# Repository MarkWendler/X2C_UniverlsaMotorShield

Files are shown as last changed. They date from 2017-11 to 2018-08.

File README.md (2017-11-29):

# X2C_Motorshield
Universal motor driver board for X2C Development board

## Planned Main features
* BLDC, PMSM motor drive
* 2 Phase Current sense
* 3 Phase voltage sense
* Led feedback from PWM outputs                                                                   
* Over current protection
* Optional Motor supply (Up to 48V Not)
* Interface to HALL sensor and Quadrature Encoder
* DC common current sens
* External OPAMP
* CAN Bus

## Recommended parts
* MOSFET:	DMT4002LPS			http://www.diodes.com/_files/datasheets/DMT4002LPS.pdf						
* Mosfet Driver:	MIC4607			http://www.microchip.com/wwwproducts/en/MIC4607						
* Current and voltage sense:	MCP6024 http://www.microchip.com/wwwproducts/en/MCP6024						
* 5V Supply LDO:	MCP1790/91									
* 8-12V LDO:	MIC5233 (Adjustable)			http://ww1.microchip.com/downloads/en/DeviceDoc/mic5233.pdf						
* CAN transciever:	ATA6563

### Pinout
Coming soon

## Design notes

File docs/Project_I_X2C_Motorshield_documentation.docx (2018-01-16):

# X2C Universal motor shield

Authors:

Csányi Dániel (Obuda university)

Mark Wendler

mark.wendler@microchip.com

Christoph Baumgartner

christoph.baumgartner@microchip.com

V 0.1

15.01.2018

RECOMMENDED READING

X2C development board docs:

- http://x2c.microstickplus.com/home

# 1 Introduction

With the X2C motor driver development board we can control a BLDC (brushless DC) motor or a permanent magnet synchronous motor (PMSM). This Motorshield is a separate board from the X2C+ Development Board and this board is not contained microcontroller. The control unit is a X2C+ development board, integrated Pickit on Board programmer/debugger support. The main motor control device unit is a 16-bit dsPIC33EP256MC502.

This document is showed the Motorshield board without the X2C features.

  1.1 Features overview

The key features of this board include the following:

- Motor Control Interfaces
- Three-phase inverter bridge with a power rating 48V/15A
- Hall sensors/quadrature encoder interface for sensored motor control
- Phase voltage feedback for sensorless BLDC operation
- DC bus current sesnse resistor for single shunt vector control
- Phase current sense resistor for dual shunt vector control
- Overcurrent protection
- Support for dsPIC DSCs with internal and external op amps
- Input/Output Control Switches
- LED indicators for EN/FLT
- LED indicators for PWM input
- Jumpers for sense
- Communication ports
- CAN interface port
- Power Supply Connectors
- 24V power input connector (Shield)
- Test Points

# 2 Hardware overview

This part describes the hardware components of the X2C Motorshield. The Motorshield panel works only with the X2C+ Development Board. X2C Development board is the main control unit to provide the control signals for the motor shield.

Topics covered include:

- The schematic circuit (Attached in the supplement)
- X2C board
- Parts of shield
- Pin configuration
- Board connectors

## 2.1 X2C Board

X2C+ Development Board is a cost-effective development board. The Development Board is designed to provide designers with an easy to use, economical development environment for 8 bit PIC Microcontrollers (PIC16F1885x and PIC18F2xK40), 16-bit dsPIC Enhanced Digital Signal Controllers (dsPIC33E), 16 bit PIC Enhanced Microcontrollers (PIC24E) and 32 bit PIC Microcontrollers (PIC32MX1, PIC32MM) manufactured in 28-pin SPDIP packing. It’s the perfect solution to those looking for a low-cost, easy-to-use development platform.

Some features:

- Onboard programmer/debugger PKOB
- Onboard peripherals
- No external power supply needed
- Suitable size
- Low cost

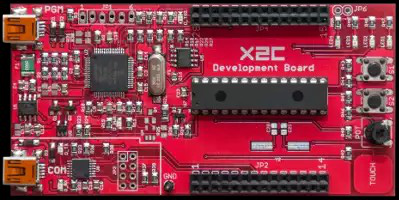
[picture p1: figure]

1. picture: X2C Development Board

The development Board is compatible with MPLAB X IDE. The software can run on PC to develop applications. It works at easy as Plug and Play, only connect the device to the PC and download the program to X2C. The Motorshield is had to connect to X2C Development Board that it is would be work.

## 2.2 Parts of shield

The schematic circuit to separate into some main subunits according to their function.

These subunits:

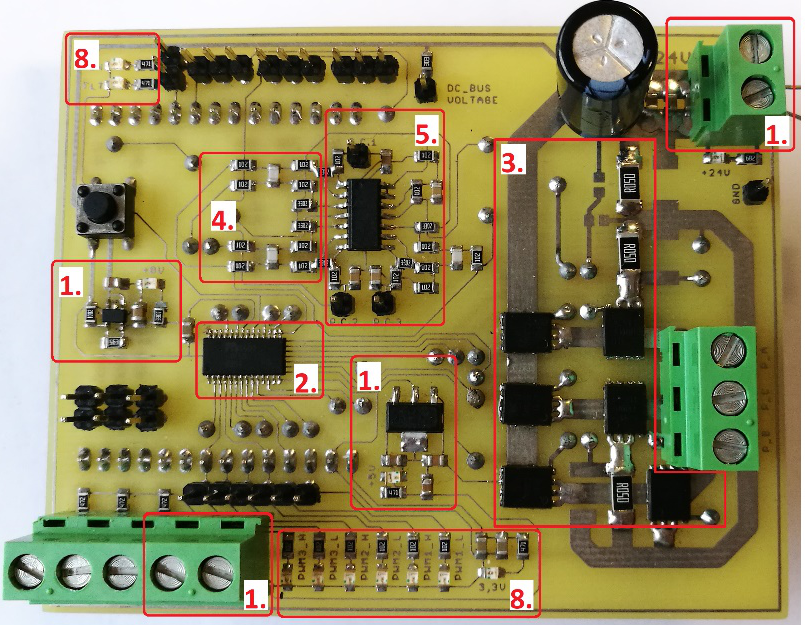
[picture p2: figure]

1. Supply

2. picture: Parts of Motorshield

2. Mosfet driver
3. Output stage
4. Phase voltage feedback
5. Current gain
6. Hall and QEI sensor

(on the other side of shield)

7. CAN Bus

(on the other side of shield)

8. Supply and output feedbacks

### Supply

External supply up to 48V is required, because high output power is needed. The capacitors stabilize the voltage and filter external noises.

The second supply convert the voltage to 5V from 24V. The MCP1790 regulator provides up to 70 mA of current. The regulator has a tight tolerance output voltage load regulation of ±0.2% and a very good line regulation at ±0.0002%/V. The regulator output is stable with electrolytic capacitors.

Voltage level | Voltage source | User part
24V | External | MOSFET
8V | Regulator | MOSFET driver
5V | Regulator | Leds, CAN, Motor sensors (CAN, HALL)
3.3V | X2C | X2C, driver’s FLT pin, Current gain

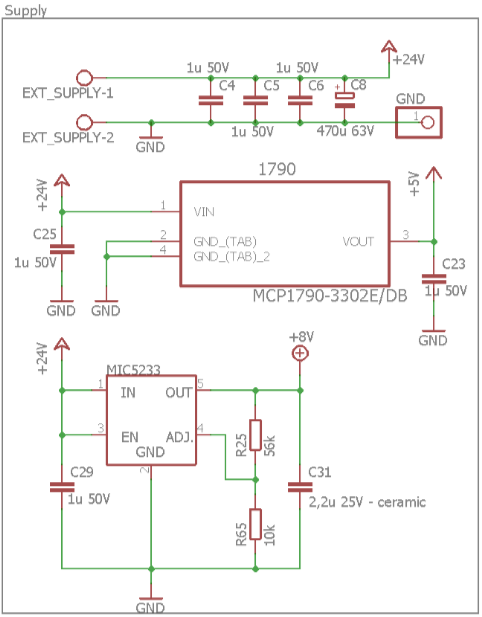
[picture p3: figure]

3. picture: Supply and regulators

The third voltage is the 8V, that use to Mosfet driver’s input voltage. The MIC5233 is a 100mA highly accurate, low dropout (270mV at 100mA) regulator with high input voltage. It only requires a 2.2uF capacitor for stability.

The sensors use a fourth voltage level – 3.3V, that support the X2C board.

### Mosfet driver

The three-phase Mosfet driver is a MIC4607. It features adaptive dead time and fast (35ns) propagation delay time and designed to independently drive six N-channel MOSFETs in a three phase bridge. Single PWM inputs can be separate high and low drive generated internally. High- and low-side outputs are guaranteed to not overlap in either mode. The driver includes overcurrent protection as well as a high-voltage internal diode that charges the high-side gate drive bootstrap capacitor. The programmable overcurrent protection circuit turns off all outputs during an overcurrent fault. Undervoltage protection is provided on both the low- and high side drivers. The input voltage is 8V from the regulator. The small switcing times that about 35ns, become a fast driver.

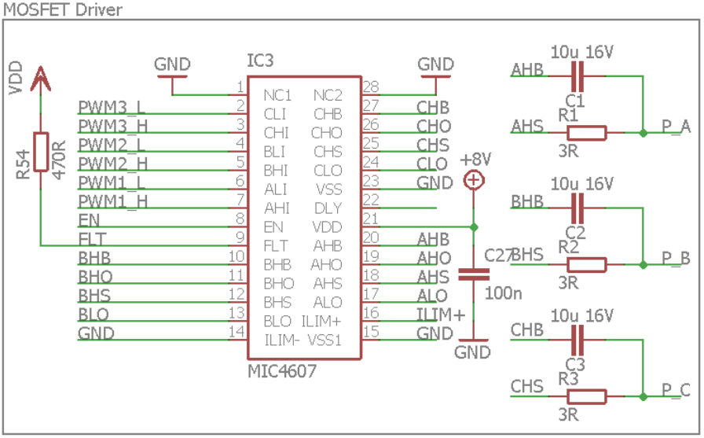
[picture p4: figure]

4. picture: MOSFET driver

There is one external enable pin that controls all three phases. A logic high on the enable pin (EN) allows for startup for all phases and normal operation. Conversely, when a logic low is applied on the enable pin, all phases turn-off and the device enters a low current shutdown mode. All outputs (xHO and xLO) are pulled low when EN is low.

FLT pin open-drain output is pulled low while the gate drive outputs are latched off after an over-current condition. It will de-assert once the DLY pin has reached the V_(DLY+) threshold and a rising edge occurs on any LI pin. During normal operation, the internal pull-down MOSFET is of the pin is high impedance. A pull-up resistor must be connected to this pin.

All input pins (xLI and xHI) are referenced to the VSS pin. The MIC4607 has a TTL-compatible input range and can be used with input signals with amplitude less than the supply voltage. The threshold level is independent of the VDD supply voltage and there is no dependence between I_(VDD) and the input signal amplitude. This feature makes the driver an excellent level translator that will drive high level gate threshold MOSFETs from low-voltage PWM IC.

On the right side of the picture the external output signals attached to driver via bootstrap capacitor and a resistor. The ceramic condensator filter the noises.

Pin number | Pin Name | Pinout description
2 | CLI | Low-Side Input for Phase C
3 | CHI | High-Side Input for Phase C
4 | BLI | Low-Side Input for Phase B
5 | BHI | High-Side Input for Phase B
6 | ALI | Low-Side Input for Phase A
7 | AHI | High-Side Input for Phase A
8 | EN | Active high enable input
9 | FLT | Fault/pin goes low when overcurrent
11 | BHO | Phase B High Side Drive Output
13 | BLO | Phase B Low Side Drive Output
14 | ILIM- | Differential Current-Limit Input (most -)
16 | ILIM+ | Differential Current-Limit Input (most +)
17 | ALO | Phase A Low Side Drive Output
19 | AHO | Phase A High Side Drive Output
21 | VDD | Input Supply
22 | DLY | Fault Delay/connect to GND
24 | CLO | Phase C Low Side Drive Output
26 | CHO | Phase C High Side Drive Output

### Output stage

The output stage principle is a three phase voltage inverter circuit that control the Mosfet driver. The N-channel MOSFET is a DMT4002LPS with very big continuously current (100A). This MOSFET has been designed to minimize the on-state resistance ( R_(DS(ON)) ) and yet maintain superior switching performance, making it ideal for high efficiency power management applications.

Main features:

- Unclamped Inductive Switching
- Thermally Efficient Package
- High conversion Efficiency
- Low R_(DS(ON))
- Small Package Profile

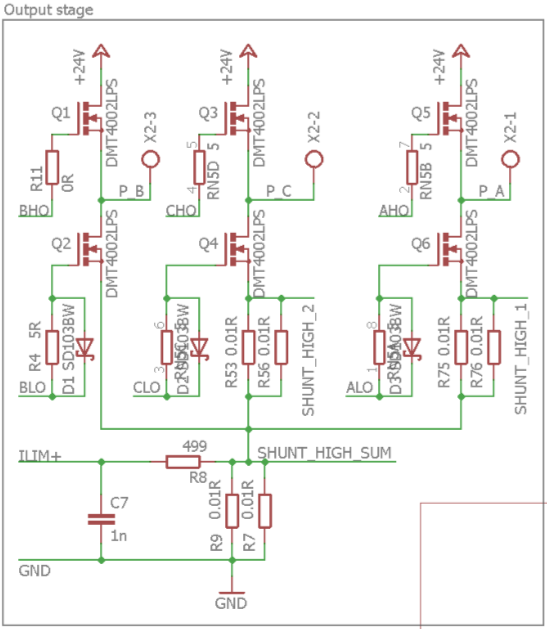
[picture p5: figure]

5. picture: Output stage

The ILIM+ and ILIM- pins provide a Kelvin-sensed circuit that monitors the voltage across an external current sense resistor. This resistor is typically connected between the source pins of all three low-side MOSFETs and power ground. If the peak voltage across this resistor exceeds the U_(ILIM+) threshold, it will cause all six outputs to latch off when the current more than 40A.

I_(max) =(U_(ILIM+))/(R_(shunt))=(200 mV)/(0.005 Ω)=40 A

Main characteristics
Characteristics | | Symbol | Value | Units
Max Drain-Source Voltage | | U_(DSS) | 40 | V
Max Gate-Source Voltage | | U_(GSS) | ±20 | V
Max Continuous Drain Current, U_(GS) =10V | T_c = +25 ℃ T_c = +70 ℃ | I_D | 100 100 | A A
Drain-Souce Breakdown Voltage | U_(GS) =0V | BU_(DSS) | 40 | V
Static Drain-Source On-Resistance | U_(GS) =10V, I_D =25A | R_(DS(ON)) | 1.3 | mΩ
Rising Overcurrent Threshold | | U_(ILIM+) | 200 | mV

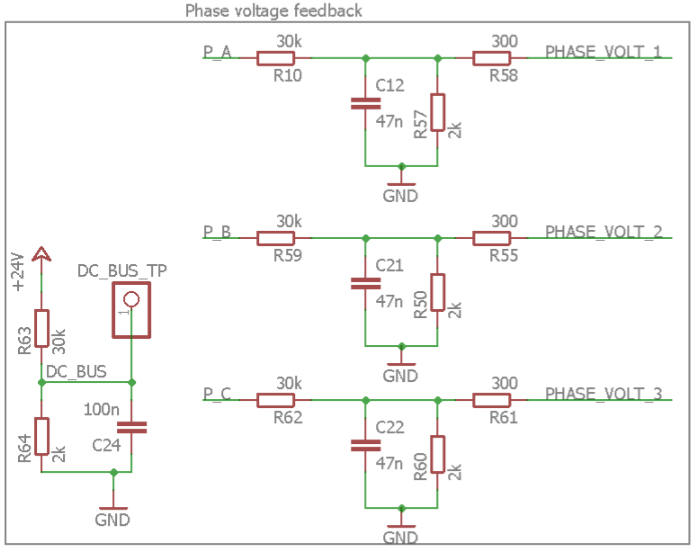
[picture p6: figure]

### Phase voltage feedback

6. picture: Phase voltage feedback

The output signals are feedbacked by resistance divider. These feedbacks are connected to dsPIC microcontroller and it is processed the analog signals. The microcontroller is measured the voltages, because if the motor hasn’t got sensors, the control is generated from the phase voltages. This part is contained a supply to DC BUS. The X2C is communicated and is exchanged data with the Motorshield panel. The data transfer is operated as serial. The data is modulated to the DC BUS.

### Current gain

The MCP6024 is rail-to-rail input and output operational amplifiers with high performance.

Main features:

- Wide Bandwidth: 10 MHz
- Low Noise
- Low Offset Voltage
- Low Supply Current
- Power supply range: 2.5V to 5.5V

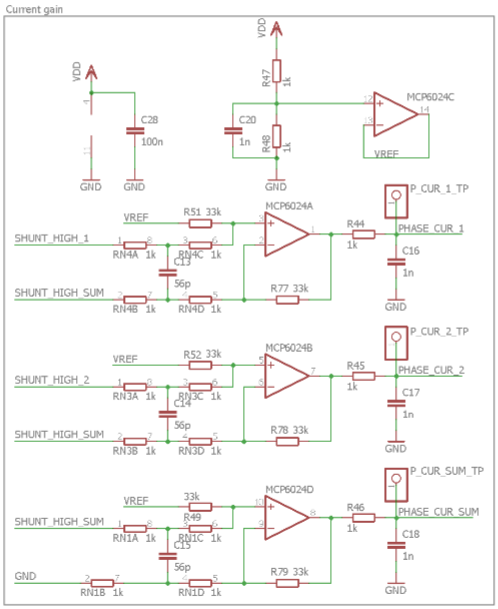
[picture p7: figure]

7. picture: Current gain

On low-side parts are measured the currents on A, C shunts and common sources level. . From the sum level is operated the overcurrent protection. In order to prevent damage and/or improper operation of these amplifiers, the circuit must limit the voltages at the input pins. The two resistros on the input side, limit the possible currents in or out of the input pins.

Circuit A (VDD to amplifier) sets the operational amplifier at its minimum noise gain. The resistor divider produces any desired reference voltage within the output voltage range of the operational amplifier. The operational amplifier buffers that reference voltage. Circuit B (Uref) uses the minimum number of components and operates as a comparator, but it may draw more current.

### Hall and QEI sensor

The most common way to control a BLDC motor is to use Hall sensors to determine the rotor position. The control system senses the rotor position and the proper voltage pattern is applied to the motor.

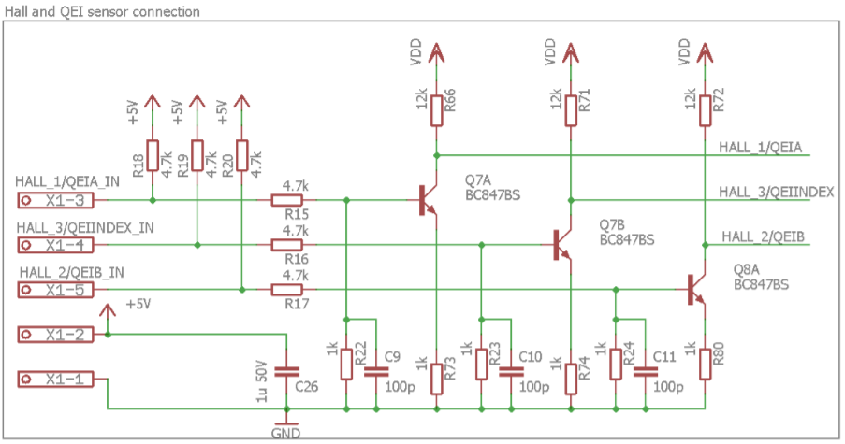
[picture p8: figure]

8. picture: Hall and QE sensor's circuit

A quadrature encoder is a type of incremental encoder used in many general automation applications where sensing the direction of movement is required. If your motor is used a large vector, a bearingless or magnetic encoder will provide the most reliable feedback. This part of circuit is contained a 5V output supply connectors.

### CAN Bus

The ATA6563 is a high-speed CAN transceiver that provides an interface between a controller area network (CAN) protocol controller and the physical two-wire CAN bus. The transceiver is designed for high-speed Can applications and providing differential transmit and receive capabillity to a CAN protocol controller.

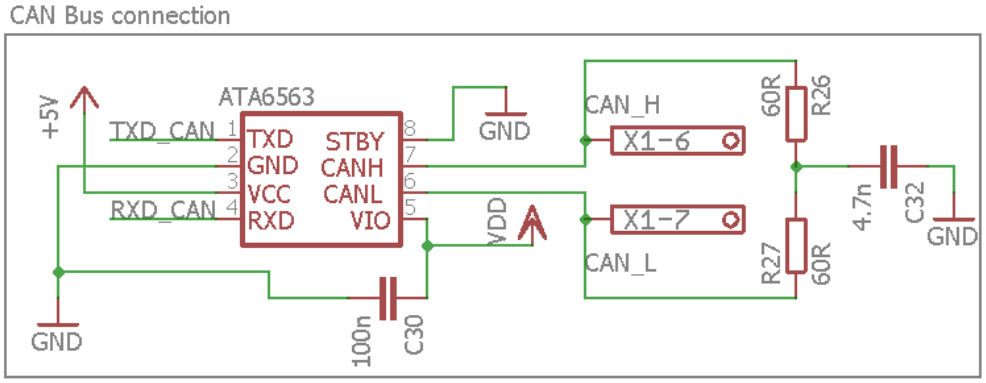
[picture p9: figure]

9. picture: Can bus circuit

The pin 5 is the VIO pin and should be connected to the microcontroller supply voltage. This allows direct interfacing to microcontrollers with supply voltages down to 3V and adjusts the signal levels of the TXD, RXD, and STBY pins to I/O levels of the microcontroller.

## 2.3 Pin configuration

Summarizes the Pin configuration for the X2C Motorshield MIC4607 driver. This table shows the dsPIC Digital Signal Controller Pin configuration. These Pins use the main board, the MOSFET driver or part of the Motorshield panel.

dsPIC | | Motorshield | | User tool | Description
Pin number | Pin name | Pin number | Signal name
1 | MCLR | L1 | GND | Used both panel | Connect to GND
2 | AN0/RA0 | L2 | Phase_I_V_2 | Used both panel | Measure voltage on Phase B or current on Phase C
3 | AN1/ RA1 | L3 | POT | X2C Board | Potenciometer
4 | PGED3/VREF-/AN2/RB0 | L4 | Phase_I_V_3 | Used both panel | Measure voltage on Phase C or current on common source point
5 | PGEC3/VREF+/RPI33/RB1 | L5 | PGEC | No connection
6 | PGEC1/AN4/RPI34/RB2 | L6 | Phase_I_V_1 | Used both panel | Measure voltage on Phase A or current on Phase A
7 | PGED1/AN5/RP35/RB3 | L7 | DC_BUS | Motorshield panel | Communicating supply
8 | VSS | L8 | GND | Used both panel | Connect to GND
9 | RA2 | L9 | EN | Motorshield panel | Active high enable input
10 | RA3 | L10 | FLT | Motorshield panel | Fault/pin goes low when overcurrent
11 | RP36/RB4 | L11 | | No connection
12 | RP20/RA4 | L12 | | No connection
13 | VDD | L13 | NC | X2C Board | Not connected
14 | PGED2/RP37/RB5 | L14 | RXD_CAN | Motorshield panel | Serial receive pin from MCU
15 | AVDD | R1 | VDD | X2C Board | Supply as 3.3V
16 | AVSS | R2 | GND | Used both panel | Connect to GND
17 | RPI47/PWM1L /RB15 | R3 | PWM1_L | Motorshield panel | Low-Side Input for Phase A
18 | RPI46/PWM1H/RB14 | R4 | PWM1_H | Motorshield panel | High-Side Input for Phase A
19 | RPI45/PWM2L/RB13 | R5 | PWM2_L | Motorshield panel | Low-Side Input for Phase B
20 | RPI44/PWM2H/RB12 | R6 | PWM2_H | Motorshield panel | High-Side Input for Phase B
21 | RP43/PWM3L/RB11 | R7 | PWM3_L | Motorshield panel | Low-Side Input for Phase C
22 | RP42/PWM3H/RB10 | R8 | PWM3_H | Motorshield panel | High-Side Input for Phase C
23 | VCAP | R9 | NC | No connection
24 | VSS | R10 | VSS | Used both panel | Connect to ground
25 | TMS/RP41/RB9 | R11 | TXD_CAN | Motorshield panel | Serial transmit pin from MCU
26 | TCK/RP40/RB8 | R12 | HALL_1/QEIA | Motorshield panel | HaLL and QE input for Phase A
27 | RP39/RB7 | R13 | HALL_2/QEIB | Motorshield panel | HaLL and QE input for Phase B
28 | PGEC2/RP38/RB6 | R14 | HALL_3/ QEIINDEX | Motorshield panel | HaLL and QE input for INDEX

## 2.4 Board connectors

The next tables describes the hardware connections.

Number | Designator | Description
1 | J1 | Input power supply connector
2 | J2 | Motor power connector
3 | J3 | HaLL connector
4 | J4 | Output low voltage connector

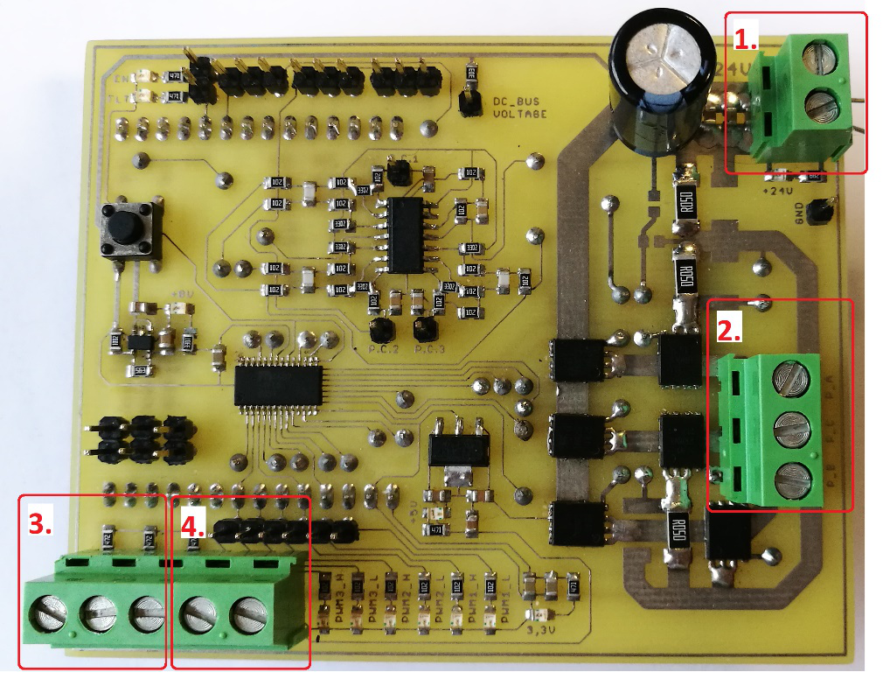
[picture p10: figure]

10. picture: Connectors of Motorshield

The panel is contained various test points, that next table is showed:

Test points | Description
EN | Enable pin
FLT | Fault pin
DC BUS Voltage | DC BUS Voltage level
P.C.1 | Phase current 1
P.C.2 | Phase current 2
P.C.3 | Phase current sum
PWM1L | PWM low-side input level for Phase A
PWM1H | PWM high-side input level for Phase A
PWM2L | PWM low-side input level for Phase B
PWM2H | PWM high-side input level for Phase B
PWM3L | PWM low-side input level for Phase C
PWM3H | PWM high-side input level for Phase C
GND | Analog ground

These test points are used to measure the values with oscilloscope.

## 2.5 User interface hardware

### Jumpers

Designator | Position | Description
JP1 | 1-2 | Connects current sense to phase 1 to monitor
| 2-3 | Connects voltage sense to phase 1 to monitor
JP2 | 1-2 | Connects current sense to phase 2 to monitor
| 2-3 | Connects voltage sense to phase 2 to monitor
JP3 | 1-2 | Connects current sum sense to monitor
| 2-3 | Connects voltage sense to phase 3 to monitor

### Leds

The Motorshield has LED indicators for the supplies, PWM and FLT/EN signals. The instantaneous signals can easily check with these LEDs. Picture of 2. part 8. is showed the LEDs on board.

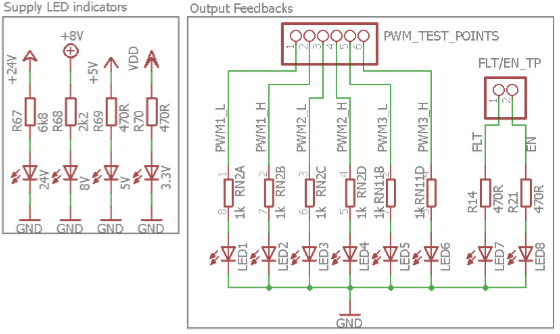
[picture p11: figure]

11. picture: LEDs of Motorshield

Leds name | Description
EN | Enable status LED
FLT | Fault status LED
PWM1-6 | LEDs, which indicate the PWM pin status
24V | Power-on status LED
8V | Power-on status LED, which indicates the status of the 8V regulator
5V | Power-on status LED, which indicates the status of the 5V regulator
3.3V | X2C power-on status LED

# 3 Operating requirements

To set up and run the board, following items are recommended:

1. MPLAB X IDE installed on the PC
2. dsPIC33EP256MC502 Digital Signal Controller
3. 24V power supply
4. BLDC or PMSM motor
5. X2C Development Board
6. X2C Motorshield Board

# 4 Electrical specifications

## 4.1 DC input ratings

Parameter | Min. | Max. | Unit
Power supply | 24 | 30 | V

## 4.2 DC output ratings

Parameter | Min. | Typical | Max. | Unit
Voltage | 0 | 24 | 48 | V
Current | 0 | 5 | 15 | A
Power rating | 0 | 120 | 720 | Watts

The output current is depended from the shield and other parts.

# 5 Diagram lists

# 6 Attachments

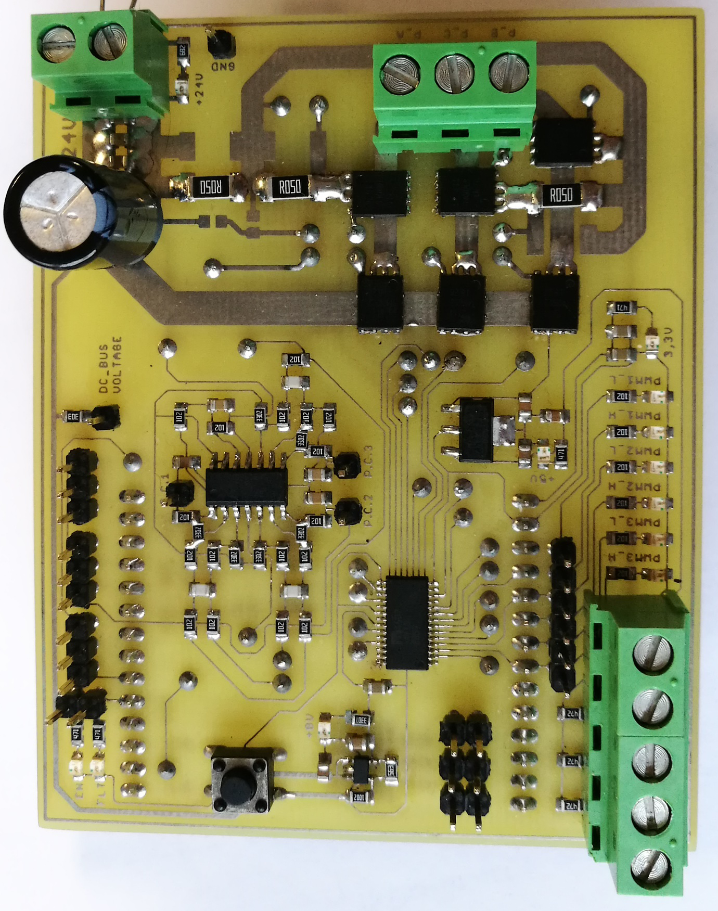
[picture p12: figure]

12. picture: X2C Motorshield

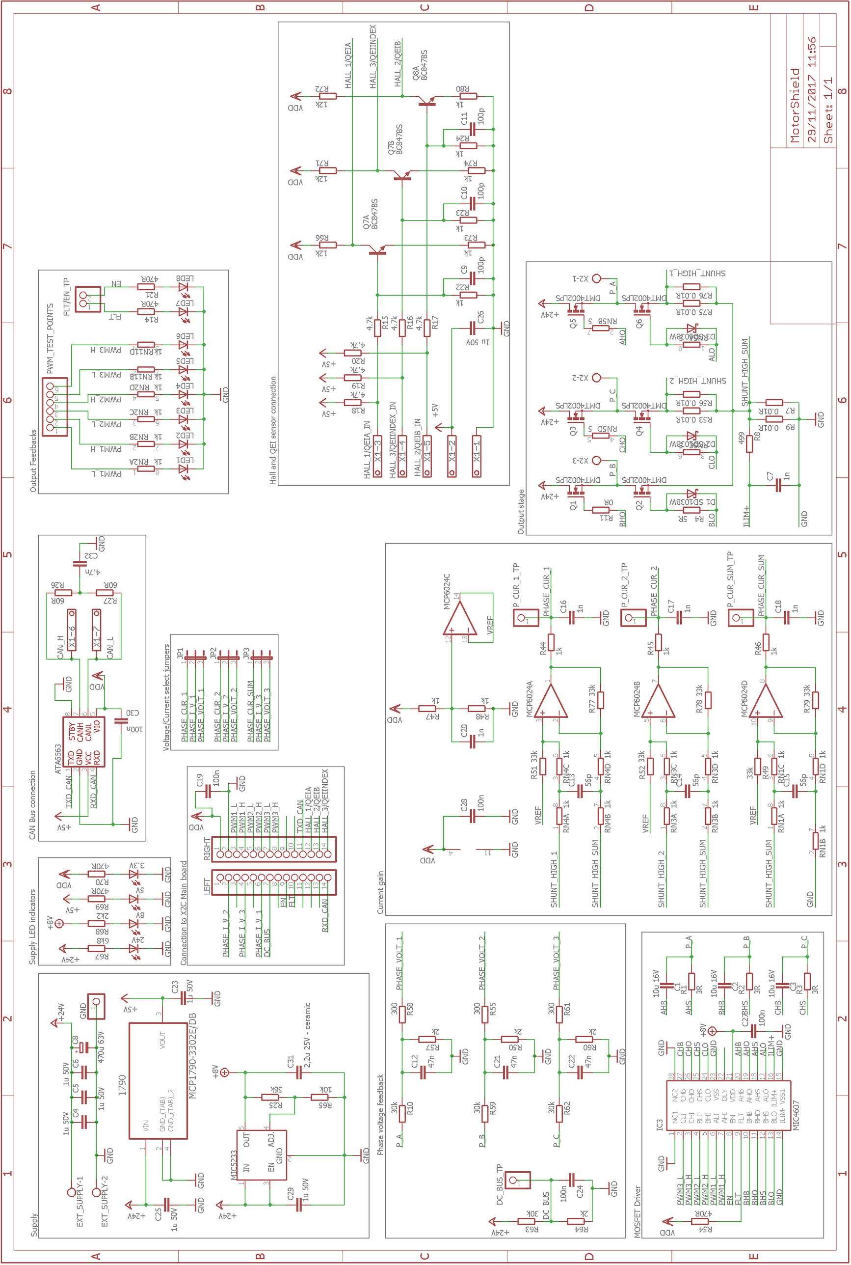
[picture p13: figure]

13. picture: The schematic circuit

# 7 Sources

High Voltage Regulator - MCP1790:

http://ww1.microchip.com/downloads/en/DeviceDoc/22075b.pdf

Voltage Regulator - MIC5233:

http://ww1.microchip.com/downloads/en/DeviceDoc/mic5233.pdf

X2C Development Board:

http://x2c.microstickplus.com/

CAN Transceiver - ATA6563:

http://ww1.microchip.com/downloads/en/DeviceDoc/20005790B.pdf

Microchip of X2C - dsPIC33EP256MC502:

http://ww1.microchip.com/downloads/en/DeviceDoc/70000657H.pdf

MOSFET driver - MIC4607:

http://ww1.microchip.com/downloads/en/DeviceDoc/20005610A.pdf

MCLV-2 Development Board:

http://ww1.microchip.com/downloads/en/DeviceDoc/DS-52080a.pdf

I/O operational amplifier - MCP6024:

http://ww1.microchip.com/downloads/en/DeviceDoc/20001685E.pdf

NPN transistor - BC847BS:

https://assets.nexperia.com/documents/data-sheet/BC847BS.pdf

N-channel MOSFET - DMT4002LPS:

https://www.diodes.com/assets/Datasheets/DMT4002LPS.pdf

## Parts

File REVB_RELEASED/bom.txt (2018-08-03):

Partlist exported from C:/Users/M18034/Google Drive/projektek/X2C_board/exp_boards/Universal/Eagle_/MotorShield.sch at 13/06/2018 17:30

Qty Value          Device                    Package      Parts                                  Description                                            EAGLEID MCHP_ID  MF MPN OC_FARNELL OC_NEWARK SPICEPREFIX TME          VALUE    
2                  PINHD-1X14                1X14         LEFT, RIGHT                            PIN HEADER                                                                                                                            
2                  PINHD-1X2                 1X02         GND, JP4                               PIN HEADER                                                                                                                            
4                  PINHD-1X3                 1X03         FLT/EN_TP, OBSRV1, OBSRV2, OBSRV3      PIN HEADER                                                                                                                            
1                  PINHD-1X4                 1X04         JP_CURRENT                             PIN HEADER                                                                                                                            
1                  PINHD-1X6                 1X06         PWM_TEST_POINTS                        PIN HEADER                                                                                                                            
3   0R             R-EU_SMDR0603_0R          R0603        R11, R13, R28                          RESISTOR, European symbol                                                                                                    0R       
1   100n           C-EUC0805                 C0805        C24                                    CAPACITOR, European symbol                                                                          C                                 
6   100nF          C-EU-SMD_0603_100NF_50V   C0603K       C5, C25, C27, C28, C29, C33            CAPACITOR, European symbol                             1204                                                                  100nF    
3   10uF           C-EU-SMD_0805_10UF_16V    C0805K       C1, C2, C3                             CAPACITOR, European symbol                             1275                                                                  10uF     
1   10uF           C-EU-SMD_1206_10UF_50V    C1206        C6                                     CAPACITOR, European symbol                             1368                                                                  10uF     
1   12,4k 1%       R-EU_SMDR0603_12,4K_1%    R0603        R67                                    RESISTOR, European symbol                              1316                                                                  12,4k 1% 
2   12k 1%         R-EU_SMDR0603_12K_1%      R0603        R6, R65                                RESISTOR, European symbol                              1317                                                                  12k 1%   
2   1k             4R-NEXB38V                EXB38V       RN2, RN11                              Array Chip Resistor                                                            unknown    unknown                                     
7   1nF            C-EU-SMD_0603_1NF_100V    C0603K       C7, C13, C14, C15, C16, C17, C18       CAPACITOR, European symbol                                                                                                   1nF      
2   1uF            C-EU-SMD_0603_1UF_10V     C0603K       C19, C26                               CAPACITOR, European symbol                             1309                                                                  1uF      
8   2,2k           4R-N2,2K                  EXBV8V_A     R10, R15, R17, R18, R34, RN1, RN3, RN4 Array Chip Resistor                                    1022                                                                  2,2k     
3   2,2k           R-EU_SMDR0603_2,2K        R0603        R47, R48, R68                          RESISTOR, European symbol                              1364                                                                  2,2k     
1   200R           4R-N200R                  EXBV8V_A     R16                                    Array Chip Resistor                                    1023                                                                  200R     
1   22k            4R-N22K                   EXBV8V_A     R19                                    Array Chip Resistor                                                                                                          22k      
7   22k 1%         R-EU_SMDR0603_22K_1%      R0603        R12, R49, R51, R52, R77, R78, R79      RESISTOR, European symbol                              1314                                                                  22k 1%   
5   22nF           C-EU-SMD_0603_22NF_16V    C0603K       C12, C20, C21, C22, C32                CAPACITOR, European symbol                             1311                                                                  22nF     
1   22pF           C-EU-SMD_0603_22PF_50V    C0603K       C4                                     CAPACITOR, European symbol                             1312                                                                  22pF     
1   330R           R-EU_SMDR0603_330R        R0603        R70                                    RESISTOR, European symbol                              1374                                                                  330R     
6   3R             R-EU_SMDR0603_3R          R0603        R1, R2, R3, R4, R29, R30               RESISTOR, European symbol                                                                                                    3R       
3   4,7uF          C-EU-SMD_0603_4,7UF_16V   C0603K       C31, C34, C35                          CAPACITOR, European symbol                             1310                                                                  4,7uF    
1   4,7uH          WE-TPC_3816_4,7UH_0,9A    WE-TPC_3816  L1                                     SMD Shielded Tiny Power Inductor                                                                                             4,7uH    
4   40V            SCHOTTKY40V               MINIMELF     D1, D2, D3, D5                         Schottky Diode                                                                                                  TMMBAT48FILM 40V      
1   470u 63V       CPOL-EUE                  PANASONIC_E  C8                                     POLARIZED CAPACITOR, European symbol                                                                C                                 
2   60R            R-EU_SMDR1206_60R         R1206        R26, R27                               RESISTOR, European symbol                                                                                                    60R      
5   680R           R-EU_SMDR0603_680R        R0603        R8, R14, R20, R21, R69                 RESISTOR, European symbol                                                                                                    680R     
2   68k 1%         R-EU_SMDR0603_68K_1%      R0603        R5, R25                                RESISTOR, European symbol                              1324                                                                  68k 1%   
1   ATA6563        ATA6563                   SOIC-8       ATA6563                                                                                                                                                             ATA6563  
3   BSS123         BSS123                    SOT23        T1, T2, T3                             N-CHANNEL MOS FET                                      1139                                                                  BSS123   
3   CLL5.08/2      AK500/2CSAVAROS_CLL5.08/2 CLL5.08/2    EXT_SUPPLY, X1, X3                     CONNECTOR                                              1029                                                                  CLL5.08/2
2   CLL5.08/3      AK500/3CSAVAROS_CLL5.08/3 CLL5.08/3    MOTOR, X4                              CONNECTOR                                              1030                                                                  CLL5.08/3
6   DMT4002LPS     BSZ105N04NS_PG-TDSON-8    PG-TDSON-8_  Q1, Q2, Q3, Q4, Q5, Q6                 OptiMOS (TM)3 Power-Transistor N-Channel, Normal level                                                                                
4   Green          LEDCHIPLED_0805_GREEN     CHIPLED_0805 3.3V, 5V, 8V, 24V                      LED                                                    1109                                                                  Green    
1   MCP16301T-E/CH MCP16301T-E/CH            SOT23-6      U$2                                    Microchip Buck regulator MCP16301                              MIC19965                                                               
1   MCP6004ST      MCP6004ST                 TSSOP14      MCP6024                                Quad Op Amp 2.7V to 6.0V Single Supply                                                                                                
1   MIC4607-1      MIC4607-1                 TSSOP28      MIC4607                                Microchip MIC4607 Datasheet                                                                                                           
1   MIC5233YM5     MIC5233YM5                TSOT23-5     U$1                                    Microchip MIC5233                                                                                                                     
6   R-EU_SMDR2512  R-EU_SMDR2512             R2512        R7, R9, R53, R56, R75, R76             RESISTOR, European symbol                                                                                                             
2   Red            LEDCHIPLED_0805_RED       CHIPLED_0805 LED7, LED8                             LED                                                    1110                                                                  Red      
6   Yellow         LEDCHIPLED_0805_YELLOW    CHIPLED_0805 LED1, LED2, LED3, LED4, LED5, LED6     LED                                                    1112                                                                  Yellow   
1   ll4148         1N4148MINIMELF            MINIMELF     D4                                     DIODE                                                  1075                                                     DL4148       ll4148

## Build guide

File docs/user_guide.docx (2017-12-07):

X2C motor shield

- introduction:
  - overview of the 3 phase motor driver shield
  - Features overview
- Hardware overview
  - The schematic circuit
  - Parts of shield
  - Pin configuration
1. Introduction

With the X2C motor driver development board we can control a BLDC (brushless DC) motor or a permanent magnet synchronous motor (PMSM). The control unit is a X2C+ development board, this is a cost effective development board with integrated Pickit on Board programmer/debugger support. The main motor control device unit is a 16-bit dsPIC33EP256MC502.

  1.1. Overview of the 3 phase motor driver shield

The board includes different circuit parts that implement these functions:

- a 3 phase inverter to control the six MOSFET
- CAN bus connection with an external device
- phase voltage feedback and current gain
- HALL sensor and quadrature encoder connection

The output parametes are U=24V and I=…..

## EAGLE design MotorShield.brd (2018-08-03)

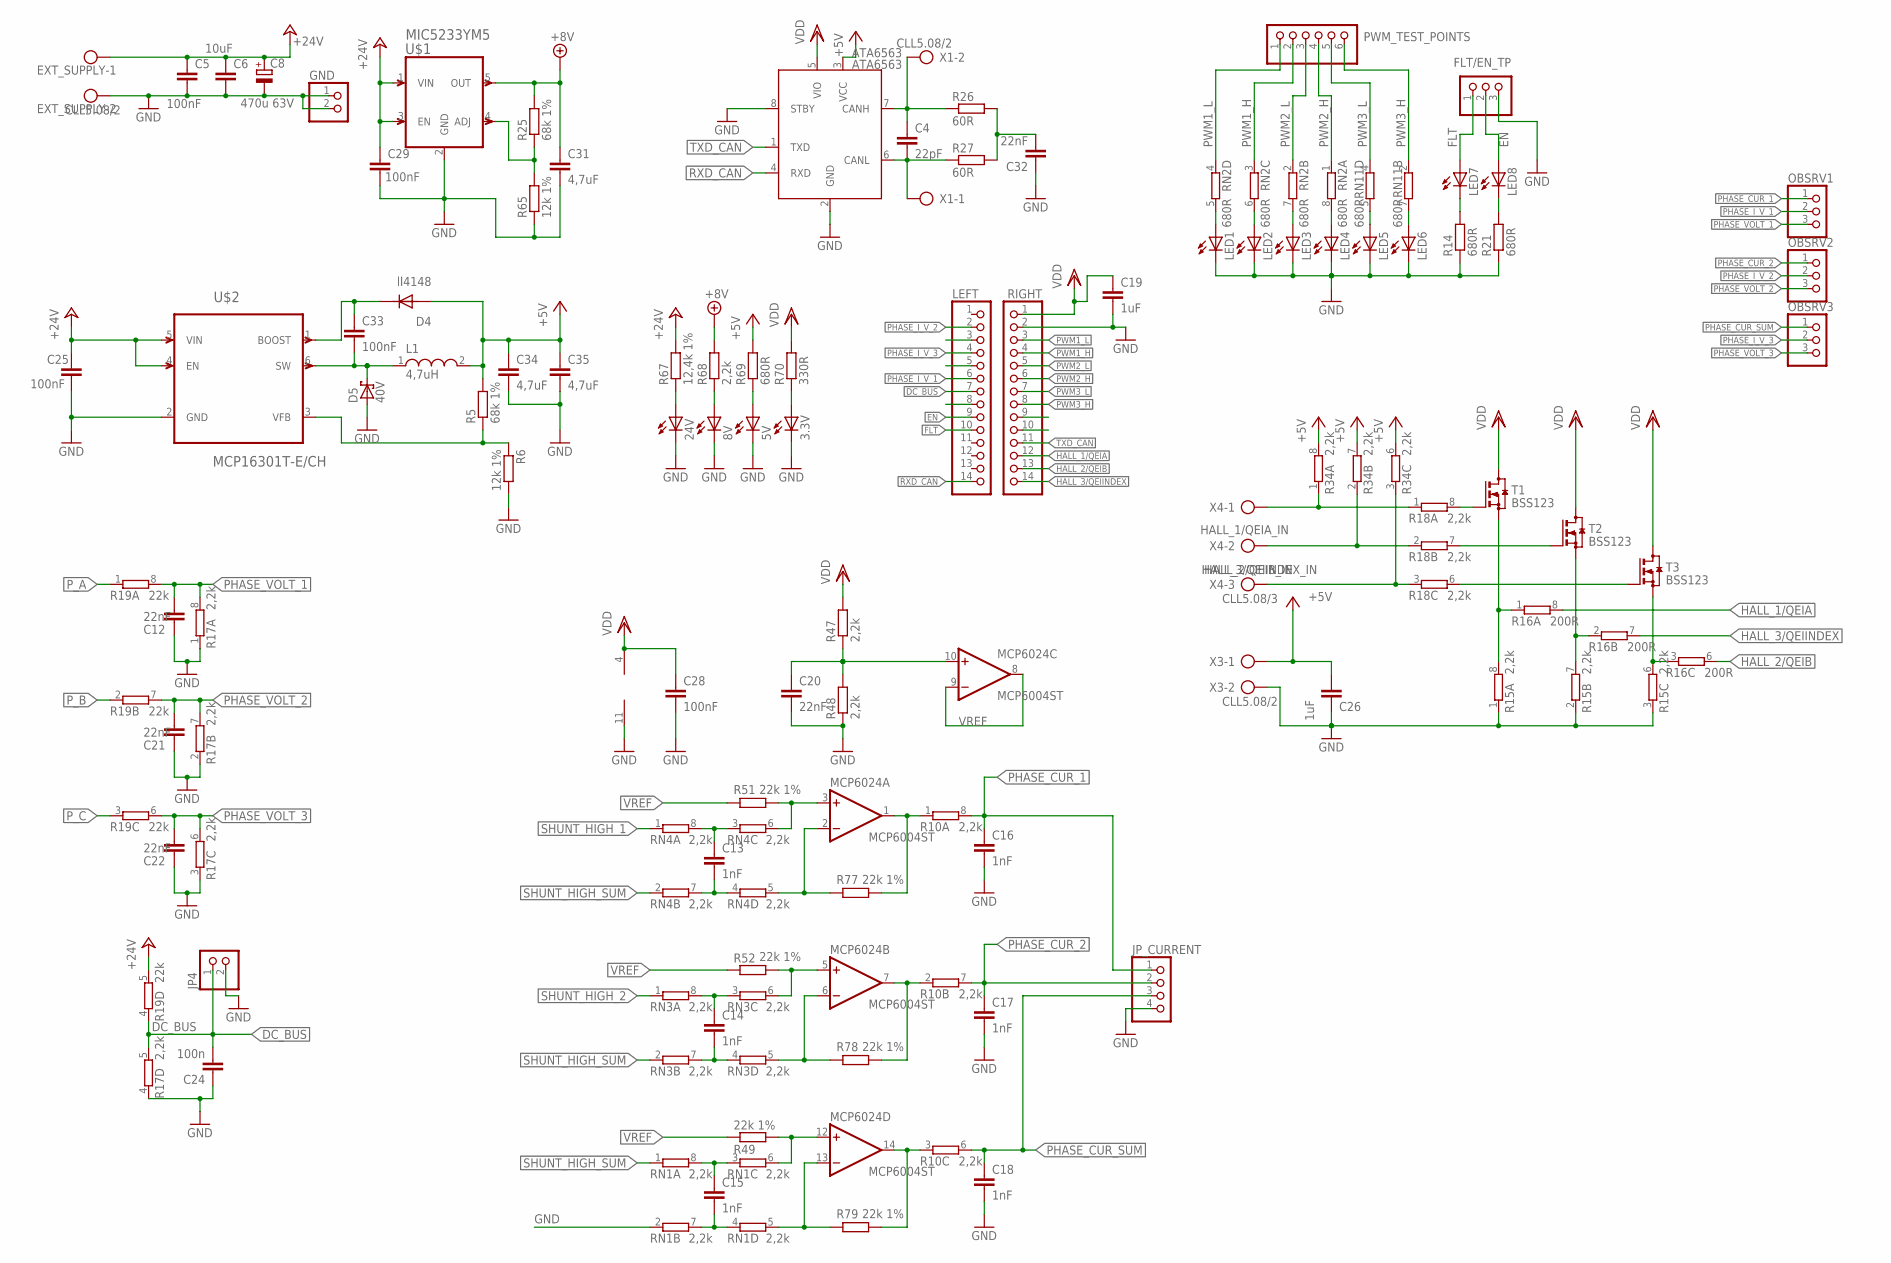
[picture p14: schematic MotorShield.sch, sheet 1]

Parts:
3.3V, 5V, 8V, 24V: Green; CHIPLED_0805
ATA6563: ATA6563; SOIC-8
C4: 22pF; C0603K
C5, C25, C28, C29, C33: 100nF; C0603K
C6: 10uF; C1206
C8: 470u 63V; PANASONIC_E
C12, C20, C21, C22, C32: 22nF; C0603K
C13, C14, C15, C16, C17, C18: 1nF; C0603K
C19, C26: 1uF; C0603K
C24: 100n; C0805
C31, C34, C35: 4,7uF; C0603K
D4: ll4148; MINIMELF
D5: 40V; MINIMELF
EXT_SUPPLY: CLL5.08/2
FLT/EN_TP: PINHD-1X3; 1X03
GND: PINHD-1X2; 1X02
JP4: PINHD-1X2; 1X02
JP_CURRENT: PINHD-1X4; 1X04
L1: 4,7uH; WE-TPC_3816
LED1, LED2, LED3, LED4, LED5, LED6: Yellow; CHIPLED_0805
LED7, LED8: Red; CHIPLED_0805
LEFT: PINHD-1X14; 1X14
MCP6024: MCP6004ST; TSSOP14
OBSRV1, OBSRV2, OBSRV3: PINHD-1X3; 1X03
PWM_TEST_POINTS: PINHD-1X6; 1X06
R5, R25: 68k 1%; R0603
R6, R65: 12k 1%; R0603
R10, R15, R17, R18, R34: 2,2k; EXBV8V_A
R14, R21, R69: 680R; R0603
R16: 200R; EXBV8V_A
R19: 22k; EXBV8V_A
R26, R27: 60R; R1206
R47, R48, R68: 2,2k; R0603
R49, R51, R52, R77, R78, R79: 22k 1%; R0603
R67: 12,4k 1%; R0603
R70: 330R; R0603
RIGHT: PINHD-1X14; 1X14
RN1, RN3, RN4: 2,2k; EXBV8V_A
RN2, RN11: 680R; EXBV8V_A
T1, T2, T3: BSS123; SOT23
U$1: MIC5233YM5; TSOT23-5
U$2: MCP16301T-E/CH; SOT23-6
X1, X3: CLL5.08/2
X4: CLL5.08/3

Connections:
+5V: ATA6563.3 (VCC), C26.1, C34.1, C35.1, D4.A, L1.2, R5.2, R34.6 (2), R34.7 (2), R34.8 (2), R69.2, X3.1
+8V: C31.1, R25.2, R68.2, U$1.5 (OUT); also elsewhere on the board
+24V: C5.1, C6.1, C8.+, C25.1, C29.1, EXT_SUPPLY.1, R19.5 (2), R67.2, U$1.1 (VIN), U$1.3 (EN), U$2.4 (EN), U$2.5 (VIN); also elsewhere on the board
CAN_H: ATA6563.7 (CANH), C4.1, R26.1, X1.2
CAN_L: ATA6563.6 (CANL), C4.2, R27.1, X1.1
DC_BUS: C24.2, JP4.1, LEFT.7, R17.5 (2), R19.4 (1)
EN: FLT/EN_TP.2, LED8.A, LEFT.9; also elsewhere on the board
FLT: FLT/EN_TP.1, LED7.A, LEFT.10; also elsewhere on the board
GND: 3.3V.C, 5V.C, 8V.C, 24V.C, ATA6563.2 (GND), ATA6563.8 (STBY), C5.2, C6.2, C8.-, C12.2, C16.2, C17.2, C18.2, C19.2, C20.2, C21.2, C22.2, C24.1, C25.2, C26.2, C28.2, C29.2, C31.2, C32.1, C34.2, C35.2, D5.A, EXT_SUPPLY.2, FLT/EN_TP.3, GND.1, GND.2, JP4.2, JP_CURRENT.4, LED1.C, LED2.C, LED3.C, LED4.C, LED5.C, LED6.C, MCP6024.11 (V-), R6.2, R14.1, R15.1, R15.2 (1), R15.3 (1), R17.1, R17.2 (1), R17.3 (1), R17.4 (1), R21.1, R48.1, R65.1, RIGHT.2, RN1.2 (1), U$1.2 (GND), U$2.2 (GND), X3.2; also elsewhere on the board
HALL_1/QEIA: R16.8 (2), RIGHT.12
HALL_1/QEIA_IN: R18.1, R34.1, X4.1
HALL_2/QEIB: R16.6 (2), RIGHT.13
HALL_2/QEIB_IN: R18.3 (1), R34.3 (1), X4.3
HALL_3/QEIINDEX: R16.7 (2), RIGHT.14
HALL_3/QEIINDEX_IN: R18.2 (1), R34.2 (1), X4.2
unnamed: MCP6024.3 (+IN), R51.2, RN4.6 (2)
unnamed: MCP6024.14 (OUT), R10.3 (1), R79.2
unnamed: MCP6024.7 (OUT), R10.2 (1), R78.2
unnamed: LED8.C, R21.2
unnamed: LED7.C, R14.2
unnamed: MCP6024.5 (+IN), R52.2, RN3.6 (2)
unnamed: C33.2, D5.C, L1.1, U$2.6 (SW)
unnamed: R25.1, R65.2, U$1.4 (ADJ)
unnamed: MCP6024.12 (+IN), R49.2, RN1.6 (2)
unnamed: R15.6 (2), R16.3 (1), T3.2 (S)
unnamed: R15.7 (2), R16.2 (1), T2.2 (S)
unnamed: R15.8 (2), R16.1, T1.2 (S)
unnamed: R18.8 (2), T1.1 (G)
unnamed: R18.7 (2), T2.1 (G)
unnamed: R18.6 (2), T3.1 (G)
unnamed: LED4.A, RN2.8 (2)
unnamed: LED3.A, RN2.7 (2)
unnamed: LED2.A, RN2.6 (2)
unnamed: 24V.A, R67.1
unnamed: 8V.A, R68.1
unnamed: 5V.A, R69.1
unnamed: 3.3V.A, R70.1
unnamed: C13.2, RN4.4 (1), RN4.7 (2)
unnamed: C13.1, RN4.3 (1), RN4.8 (2)
unnamed: MCP6024.2 (-IN), R77.1, RN4.5 (2)
unnamed: LED1.A, RN2.5 (2)
unnamed: C14.2, RN3.4 (1), RN3.7 (2)
unnamed: C14.1, RN3.3 (1), RN3.8 (2)
unnamed: LED5.A, RN11.5 (2)
unnamed: LED6.A, RN11.7 (2)
unnamed: R5.1, R6.1, U$2.3 (VFB)
unnamed: MCP6024.6 (-IN), R78.1, RN3.5 (2)
unnamed: C15.2, RN1.4 (1), RN1.7 (2)
unnamed: C15.1, RN1.3 (1), RN1.8 (2)
unnamed: MCP6024.13 (-IN), R79.1, RN1.5 (2)
unnamed: C33.1, D4.C, U$2.1 (BOOST)
unnamed: C32.2, R26.2, R27.2
unnamed: MCP6024.1 (OUT), R10.1, R77.2
unnamed: C20.1, MCP6024.10 (+IN), R47.1, R48.2
PHASE_CUR_1: C16.1, JP_CURRENT.1, OBSRV1.1, R10.8 (2)
PHASE_CUR_2: C17.1, JP_CURRENT.2, OBSRV2.1, R10.7 (2)
PHASE_CUR_SUM: C18.1, JP_CURRENT.3, OBSRV3.1, R10.6 (2)
PHASE_I_V_1: LEFT.6, OBSRV1.2
PHASE_I_V_2: LEFT.2, OBSRV2.2
PHASE_I_V_3: LEFT.4, OBSRV3.2
PHASE_VOLT_1: C12.1, OBSRV1.3, R17.8 (2), R19.8 (2)
PHASE_VOLT_2: C21.1, OBSRV2.3, R17.7 (2), R19.7 (2)
PHASE_VOLT_3: C22.1, OBSRV3.3, R17.6 (2), R19.6 (2)
PWM1_H: PWM_TEST_POINTS.2, RIGHT.4, RN2.3 (1); also elsewhere on the board
PWM1_L: PWM_TEST_POINTS.1, RIGHT.3, RN2.4 (1); also elsewhere on the board
PWM2_H: PWM_TEST_POINTS.4, RIGHT.6, RN2.1; also elsewhere on the board
PWM2_L: PWM_TEST_POINTS.3, RIGHT.5, RN2.2 (1); also elsewhere on the board
PWM3_H: PWM_TEST_POINTS.6, RIGHT.8, RN11.2 (1); also elsewhere on the board
PWM3_L: PWM_TEST_POINTS.5, RIGHT.7, RN11.4 (1); also elsewhere on the board
P_A: R19.1; also elsewhere on the board
P_B: R19.2 (1); also elsewhere on the board
P_C: R19.3 (1); also elsewhere on the board
RXD_CAN: ATA6563.4 (RXD), LEFT.14
SHUNT_HIGH_1: RN4.1; also elsewhere on the board
SHUNT_HIGH_2: RN3.1; also elsewhere on the board
SHUNT_HIGH_SUM: RN1.1, RN3.2 (1), RN4.2 (1); also elsewhere on the board
TXD_CAN: ATA6563.1 (TXD), RIGHT.11
VDD: ATA6563.5 (VIO), C19.1, C28.1, MCP6024.4 (V+), R47.2, R70.2, RIGHT.1, T1.3 (D), T2.3 (D), T3.3 (D); also elsewhere on the board
VREF: MCP6024.8 (OUT), MCP6024.9 (-IN), R49.1, R51.1, R52.1

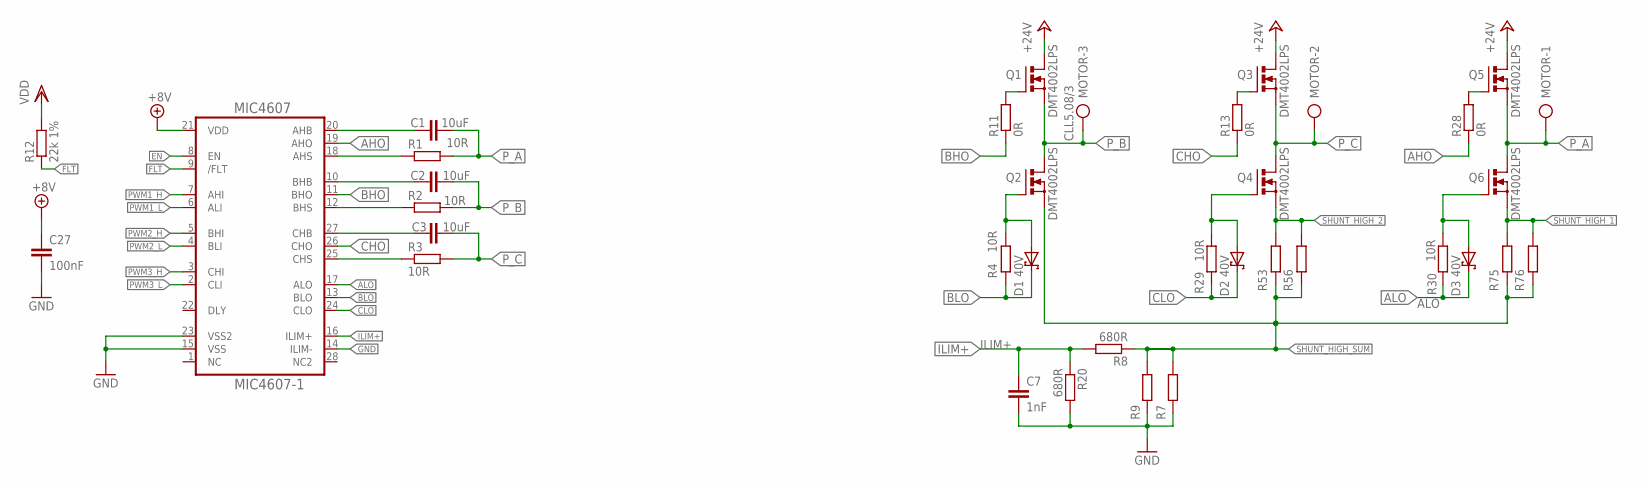
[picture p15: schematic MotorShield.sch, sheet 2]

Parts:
C1, C2, C3: 10uF; C0805K
C7: 1nF; C0603K
C27: 100nF; C0603K
D1, D2, D3: 40V; MINIMELF
MIC4607: MIC4607-1; TSSOP28
MOTOR: CLL5.08/3
Q1, Q2, Q3, Q4, Q5, Q6: DMT4002LPS; PG-TDSON-8_
R1, R2, R3, R4, R29, R30: 10R; R0603
R7, R9, R53, R56, R75, R76: R-EU_SMDR2512; R2512
R8, R20: 680R; R0603
R11, R13, R28: 0R; R0603
R12: 22k 1%; R0603

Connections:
+8V: C27.1, MIC4607.21 (VDD); also elsewhere on the board
+24V: Q1.5 (D), Q1.6 (D), Q1.7 (D), Q1.8 (D), Q1.TH (D), Q3.5 (D), Q3.6 (D), Q3.7 (D), Q3.8 (D), Q3.TH (D), Q5.5 (D), Q5.6 (D), Q5.7 (D), Q5.8 (D), Q5.TH (D); also elsewhere on the board
AHB: C1.1, MIC4607.20 (AHB)
AHO: MIC4607.19 (AHO), R28.1
AHS: MIC4607.18 (AHS), R1.1
ALO: D3.C, MIC4607.17 (ALO), R30.2
BHB: C2.1, MIC4607.10 (BHB)
BHO: MIC4607.11 (BHO), R11.1
BHS: MIC4607.12 (BHS), R2.1
BLO: D1.C, MIC4607.13 (BLO), R4.1
CHB: C3.1, MIC4607.27 (CHB)
CHO: MIC4607.26 (CHO), R13.1
CHS: MIC4607.25 (CHS), R3.1
CLO: D2.C, MIC4607.24 (CLO), R29.2
EN: MIC4607.8 (EN); also elsewhere on the board
FLT: MIC4607.9 (/FLT), R12.1; also elsewhere on the board
GND: C7.2, C27.2, MIC4607.14 (ILIM-), MIC4607.15 (VSS), MIC4607.23 (VSS2), R7.1, R9.1, R20.2; also elsewhere on the board
ILIM+: C7.1, MIC4607.16 (ILIM+), R8.2, R20.1
unnamed: Q1.4 (G), R11.2
unnamed: Q3.4 (G), R13.2
unnamed: Q5.4 (G), R28.2
unnamed: D1.A, Q2.4 (G), R4.2
unnamed: D2.A, Q4.4 (G), R29.1
unnamed: D3.A, Q6.4 (G), R30.1
PWM1_H: MIC4607.7 (AHI); also elsewhere on the board
PWM1_L: MIC4607.6 (ALI); also elsewhere on the board
PWM2_H: MIC4607.5 (BHI); also elsewhere on the board
PWM2_L: MIC4607.4 (BLI); also elsewhere on the board
PWM3_H: MIC4607.3 (CHI); also elsewhere on the board
PWM3_L: MIC4607.2 (CLI); also elsewhere on the board
P_A: C1.2, MOTOR.1, Q5.1 (S), Q5.2 (S), Q5.3 (S), Q6.5 (D), Q6.6 (D), Q6.7 (D), Q6.8 (D), Q6.TH (D), R1.2; also elsewhere on the board
P_B: C2.2, MOTOR.3, Q1.1 (S), Q1.2 (S), Q1.3 (S), Q2.5 (D), Q2.6 (D), Q2.7 (D), Q2.8 (D), Q2.TH (D), R2.2; also elsewhere on the board
P_C: C3.2, MOTOR.2, Q3.1 (S), Q3.2 (S), Q3.3 (S), Q4.5 (D), Q4.6 (D), Q4.7 (D), Q4.8 (D), Q4.TH (D), R3.2; also elsewhere on the board
SHUNT_HIGH_1: Q6.1 (S), Q6.2 (S), Q6.3 (S), R75.2, R76.2; also elsewhere on the board
SHUNT_HIGH_2: Q4.1 (S), Q4.2 (S), Q4.3 (S), R53.2, R56.2; also elsewhere on the board
SHUNT_HIGH_SUM: Q2.1 (S), Q2.2 (S), Q2.3 (S), R7.2, R8.1, R9.2, R53.1, R56.1, R75.1, R76.1; also elsewhere on the board
VDD: R12.2; also elsewhere on the board

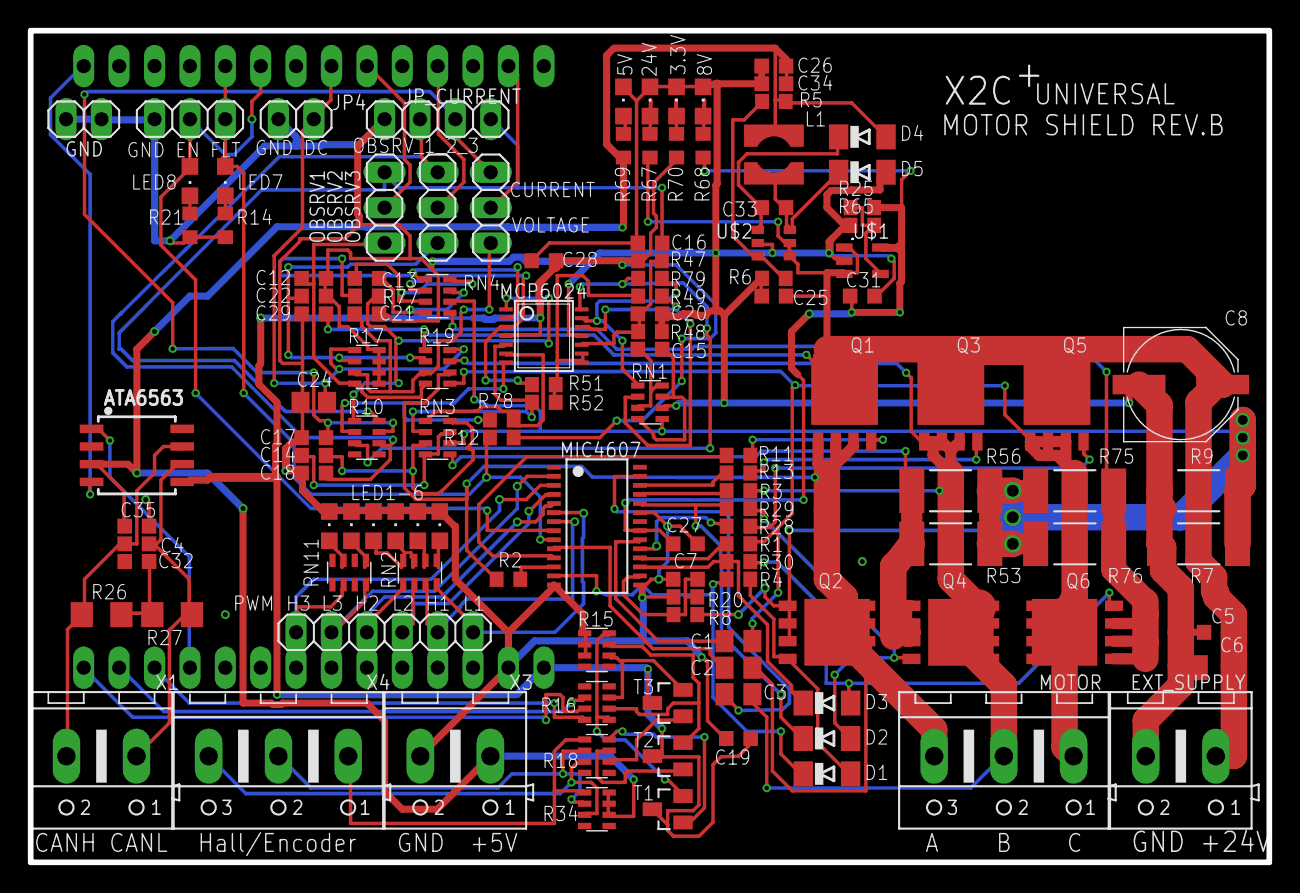
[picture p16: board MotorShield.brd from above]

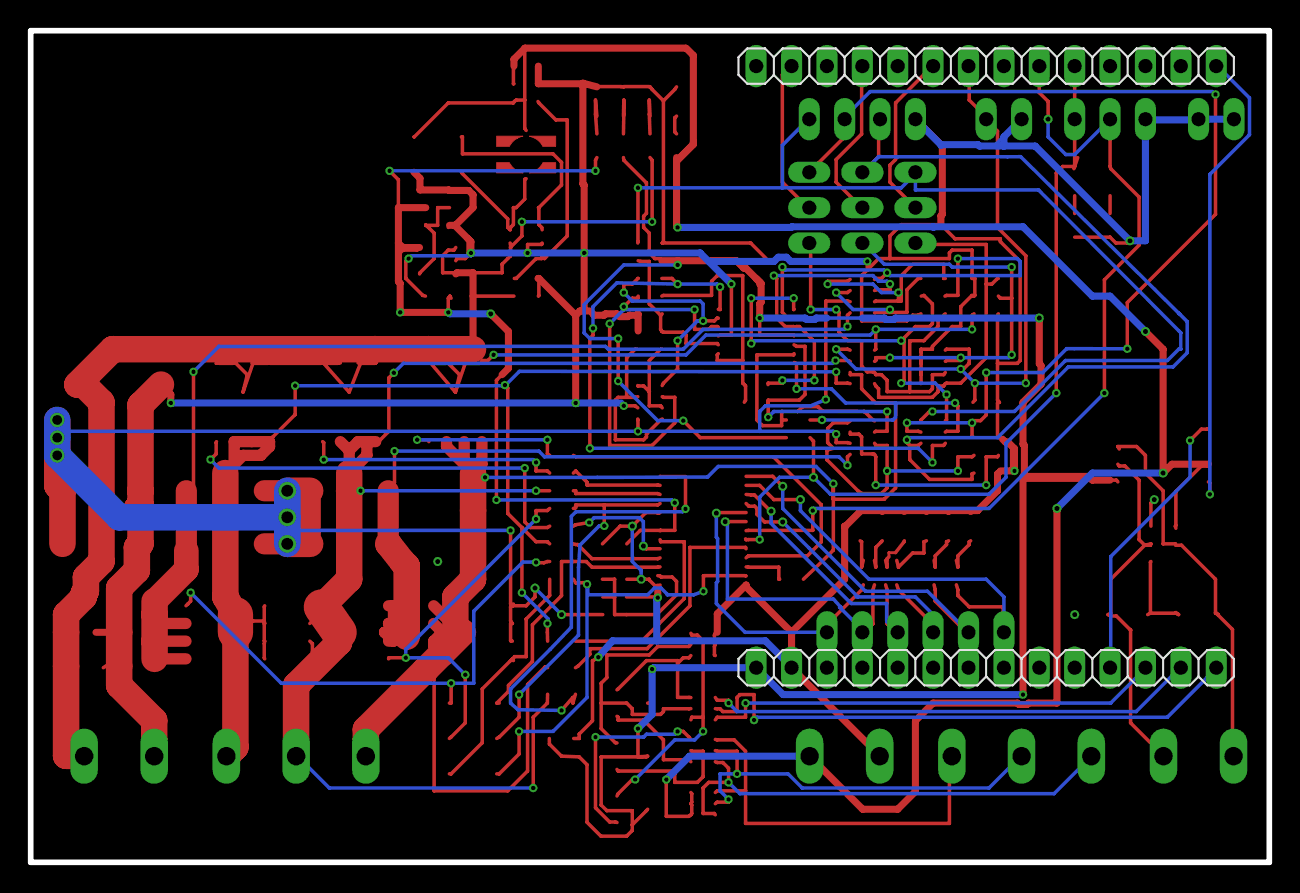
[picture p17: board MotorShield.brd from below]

Board: 2 copper layers, 88.9 x 59.7 mm, 127 parts (2 on the bottom side), 98 nets.

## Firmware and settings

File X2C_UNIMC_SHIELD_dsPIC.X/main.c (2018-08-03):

/**
  Generated Main Source File

  Company:
    Microchip Technology Inc.

  File Name:
    main.c

  Summary:
    This is the main file generated using PIC24 / dsPIC33 / PIC32MM MCUs

  Description:
    This header file provides implementations for driver APIs for all modules selected in the GUI.
    Generation Information :
        Product Revision  :  PIC24 / dsPIC33 / PIC32MM MCUs - pic24-dspic-pic32mm : v1.45
        Device            :  dsPIC33EP256MC502
    The generated drivers are tested against the following:
        Compiler          :  XC16 1.32
        MPLAB             :  MPLAB X 3.61
*/

/*
    (c) 2016 Microchip Technology Inc. and its subsidiaries. You may use this
    software and any derivatives exclusively with Microchip products.

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
    IN NO EVENT WILL MICROCHIP BE LIABLE FOR ANY INDIRECT, SPECIAL, PUNITIVE,
    INCIDENTAL OR CONSEQUENTIAL LOSS, DAMAGE, COST OR EXPENSE OF ANY KIND
    WHATSOEVER RELATED TO THE SOFTWARE, HOWEVER CAUSED, EVEN IF MICROCHIP HAS
    BEEN ADVISED OF THE POSSIBILITY OR THE DAMAGES ARE FORESEEABLE. TO THE
    FULLEST EXTENT ALLOWED BY LAW, MICROCHIP'S TOTAL LIABILITY ON ALL CLAIMS IN
    ANY WAY RELATED TO THIS SOFTWARE WILL NOT EXCEED THE AMOUNT OF FEES, IF ANY,
    THAT YOU HAVE PAID DIRECTLY TO MICROCHIP FOR THIS SOFTWARE.

    MICROCHIP PROVIDES THIS SOFTWARE CONDITIONALLY UPON YOUR ACCEPTANCE OF THESE
    TERMS.
*/

#include "mcc_generated_files/mcc.h"
#include "hardwaretweaks.h"
/*
                         Main application
 */
int main(void)
{
    // initialize the device
    SYSTEM_Initialize();
    
    MC_EN_SetLow(); //TurnOff MC output
    
    /* MCC can not configure the hardware 100% properly, so tweak it */
    hardwareTweaks();
    
    // When using interrupts, you need to set the Global Interrupt Enable bits
    // Use the following macros to:

    // Enable the Global Interrupts
    INTERRUPT_GlobalEnable();
    
    MC_EN_SetHigh(); //TurnOff MC output

    // Disable the Global Interrupts
    //INTERRUPT_GlobalDisable();

    while (1)
    {
        X2C_Communicate();
    }
}
/**
 End of File
*/

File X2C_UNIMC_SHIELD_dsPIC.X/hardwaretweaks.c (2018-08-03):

/**
 * @file
 * @brief Hardware config for X2C Universal Motor shield
 * - MCC can not setup all pripherals as needed
 * - This file are contains some hardware config tweaks top of MCC 
 * - Clock adjusted to 70Mhz
 * - A/D Sample and hold channels enable
 * - PWM 
 * @test
 * MPLABX 4.10 XC16 v1.26
 * MCLV-2
 * Hurst Brushless
 * dsPIC33EP256MC506
 * XC1065
 *
 * @author  Christiph Baumgartner
 * @author  Mark Wendler
 * @see     Christoph.Baumgartner@microchip.com
 * @see     https://www.sim2tronic.com/
 *
 * @date 20-12-2016
 */
#include "hardwaretweaks.h"

void hardwareTweaks(void){
    /*
     * Change CPU frequency to 70Mhz
     */
    
    // 7.37MHz + 23*0.00375*7.37MHz = 8MHz
    OSCTUNbits.TUN = 23; 
     // M = 70
    PLLFBD = 70;
    // N2 = 2 
    CLKDIVbits.PLLPOST = 0; 
    // N1 = 2
    CLKDIVbits.PLLPRE = 0; 
    // Switch to FRC with PLL 
    __builtin_write_OSCCONH(0x01);
    __builtin_write_OSCCONL(0x01);
    // Wait for Clock switch to occur 
    while (OSCCONbits.COSC != 0b001);
    // Wait for PLL to lock 
    while (OSCCONbits.LOCK != 1);
    /*END: Clock Config*/
    
    /*
     * Adjust Serial config to the new clock freq
     */
    U1BRG = BRGVAL;
    
    /*
     * PWM tweaks
     */
    // PWM frequency
    PHASE1 = LOOPINTCY;
    PHASE2 = LOOPINTCY;
    PHASE3 = LOOPINTCY;
    PTPER = 2 * LOOPINTCY + 1; 
    // Deadtime setting
    ALTDTR1 = DDEADTIME; 
    ALTDTR2 = DDEADTIME; 
    ALTDTR3 = DDEADTIME; 
    // low side turn on errata workaround, PDC cannot be initialized with 0 
    PDC1 = PWM_MIN; 
    PDC2 = PWM_MIN;
    PDC3 = PWM_MIN;
    
    /*
     *  QEI Config
     */
    // PPS for QEI New compatible with PIC32MK
    RPINR14bits.QEA1R = 38;
    RPINR14bits.QEB1R = 39;    

    QEI1CON = 0x0;
    QEI1CONbits.PIMOD = 6;
    // Limit count range between 0 and PULSES_PER_EREV 
    QEI1LECL = 0;
    QEI1LECH = 0;
    QEI1GECL = 200 - 1;
    QEI1GECH = 0;
    // Inverted index, QEA, QEB pins
    QEI1IOC = 0x70; 
    QEI1IOCbits.SWPAB = 1;
    // Enable digital filtering, this is a must!
    QEI1IOCbits.FLTREN = 1; 
    // QEI enable
    QEI1CONbits.QEIEN = 1;
    /* END: QEI Config*/
    
    /*
     * ADXC tweaks
     */
    // Samples CH0, CH1, CH2, CH3 simultaneously (when CHPS = 1x)
    AD1CON2bits.CHPS = 2;
    // Simultaneous Sampling enabled (only applicable when CHPS<1:0> = 01 or 1x) 
    AD1CON1bits.SIMSAM = 1;
    /* AD cnnections
     * -AN0 PhaseVolt2/SUM_Current CH1 (FIXED in 4 channel mode)
     * -AN2 PhaseCurrent2/PhaseVoltage3 CH3 (FIXED in 4 channel mode) 
     * -AN4 PhaseCurrent1/PhaseVoltage1 CH0
     * -AN11 DC_Bus_voltage CH0 
     * -AN1 POTmeter CH2 (FIXED in 4 channel mode)
     * Selected:
     * CH0 Phase_Current1/PhaseVoltage1
     * CH1 SUM_Current/PhaseVolt2
     * CH2 POT
     * CH3 PhaseCurrent2/PhaseVoltage3
     */
    AD1CHS123bits.CH123SB=0; // Selected option: AN0-CH1; AN1-CH2; AN2-CH3;
    AD1CHS0bits.CH0SA = 4; // AN4 --> Channel 0    
    AD1CON1bits.FORM = 3; // ADC-result format,  11 = Signed fractional (DOUT = sddd dddd dd00 0000, where s = .NOT.d<9>)
}

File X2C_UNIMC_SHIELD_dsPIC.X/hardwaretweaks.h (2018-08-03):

/* 
 * File:   
 * Author: 
 * Comments:
 * Revision history: 
 */

// This is a guard condition so that contents of this file are not included
// more than once.  
#ifndef HARDWARETWEAKS_H
#define	HARDWARETWEAKS_H

#include <xc.h> // include processor files - each processor file is guarded.  

#define F_FRC           8000000         /* fast RC internal oscillator frequency after tuning */
#define F_IN            F_FRC           /* FRC as input for PLL */
#define F_OSC           F_IN*70/(2*2*2)   /* fOSC = fIN*M/(N1*N2): (PLL) oscillator frequency */
#define F_CY            F_OSC/2         /* instruction cycle frequency */

#define DEADTIMESEC     0.000001    // Dead time in seconds - 1us
#define DFCY            70000000UL		// Instruction cycle frequency (Hz)
#define DTCY            (1.0/DFCY)		// Instruction cycle period (sec)
#define DDEADTIME       (unsigned int)(DEADTIMESEC*DFCY)	// Dead time in dTcys
#define MIN_DUTY        (unsigned int)(DDEADTIME/2 + 1)        // Should be >= DDEADTIME/2 for PWM Errata workaround
#define PWMFREQUENCY    10000 //10Khz
#define LOOPINTCY       (DFCY/PWMFREQUENCY)   // Basic loop period in units of Tcy

#define BAUDRATE        115200          /* baudrate for serial interface */
#define BRGVAL          ((F_CY/BAUDRATE)/4)-1 //BRGH enabled->4 divider

#define PWM_MIN     0.1 * LOOPINTCY
#define PWM_MAX     0.9 * LOOPINTCY

#define PULSE_PER_REV 1000 // ENCODER Pulses
#define N_P     5            // Electrical Pole-Pairs

void hardwareTweaks(void);

#endif

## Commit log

2017-11-29 Added Daniel's changes Fixed Mosfet Driver IC pinout Modified HALL/QIE connection And some other changes
    [MotorShield.brd, MotorShield.sch]
2018-08-03 REVB version update
    [MotorShield.brd, MotorShield.sch, bom.csv]
